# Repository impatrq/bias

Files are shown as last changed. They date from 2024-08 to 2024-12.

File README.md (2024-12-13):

# BIAS: Brain-Intelligence Artificial System
<div style="text-align: center;">
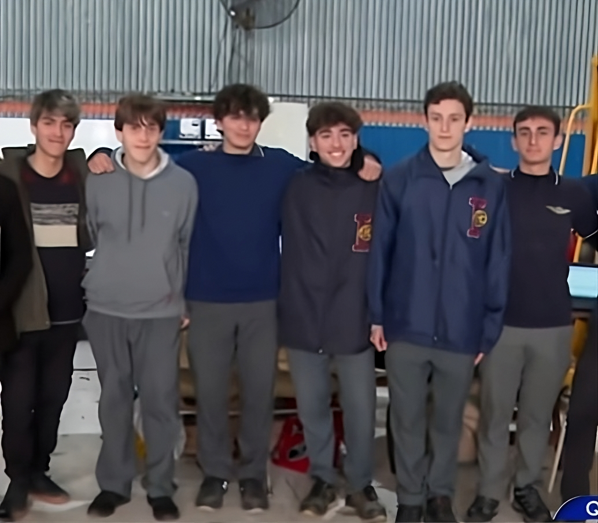
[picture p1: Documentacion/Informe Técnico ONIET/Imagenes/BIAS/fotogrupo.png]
BIAS Grupo
    
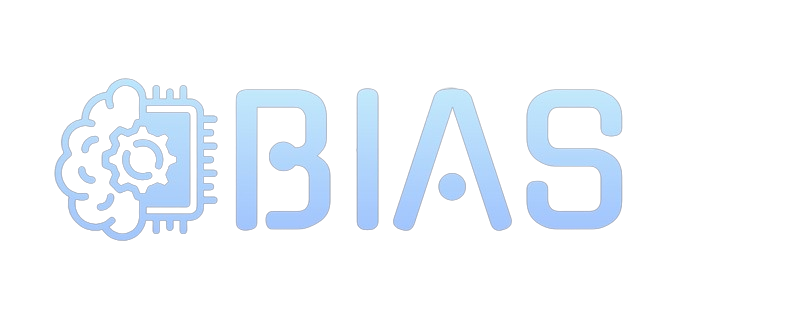
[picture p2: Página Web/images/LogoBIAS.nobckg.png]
BIAS Logo
    
</div>

[Video de Presentación](https://youtu.be/uJyJxOkbonA?si=HoqrQriFnUhKq0Xh)

## Descripción del Proyecto

BIAS es un proyecto innovador que busca mejorar la movilidad de las personas con discapacidades motrices a través de una **silla de ruedas controlada por señales cerebrales**. Utilizamos tecnología de última generación para crear un sistema que interprete las señales eléctricas del cerebro y las traduzca en movimientos precisos para la silla.

## Características principales

- **Control mental**: Movimiento de la silla mediante señales cerebrales captadas por electrodos.
- **Procesador**: Uso de una Raspberry Pi 4 para el procesamiento de las señales.
- **Motor eficiente**: Sistema de motores controlados para movimientos suaves y seguros.
- **Interfaz adaptable**: Personalización según las necesidades del usuario.

## Tecnologías utilizadas

- **Electrodos** para captar las señales cerebrales.
- **Raspberry Pi 4** para el procesamiento de datos.
- **Python y C** para el desarrollo del software y control de la IA.
- **Diseño PCB personalizado** para la integración de los componentes.
- **Motores DC** controlados por puentes H.

## Estructura del Equipo

| Integrante | Responsabilidad |
|---|---|
| **Nicolás Adell** | Programación de la IA y procesamiento de señales |
| **Luca De Blasi** | Código para los motores |
| **Ian Gil Soria** | Diseño de las placas PCB |
| **Danilo Díaz** | Desarrollo de puentes H y drivers de motor |
| **Luciano Montenegro** | Documentación y asistencia técnica |
| **Santiago Sojka** | Marketing, diseño web y estructura de la silla|

## Contacto

- **LinkTree**: [Aquí](https://linktr.ee/biasproject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)
- **Correo**: [bias.project@gmail.com](mailto:https://www.instagram.com/proyecto.bias/)
- **Instagram**: [@proyecto.bias](https://www.instagram.com/proyecto.bias)
- **Pagina Web**: [Aquí](https://sojkaa.github.io/BIAS-WEB/)

*BIAS 2024 - Todos los derechos reservados*

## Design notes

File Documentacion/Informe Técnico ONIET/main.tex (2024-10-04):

\documentclass{article} 
\UseRawInputEncoding
\usepackage[utf8]{inputenc}
\usepackage[T1]{fontenc}
\usepackage{selinput}
\usepackage[spanish]{babel}
\usepackage{hyphenat}
\usepackage{graphicx} 
\usepackage{subcaption}
\usepackage{hyperref}
\usepackage{listings}
\usepackage{xcolor}
\usepackage{float}
\usepackage[a4paper, total={6in, 9in}]{geometry}
\begin{document}
\date{} 

\begin{center}
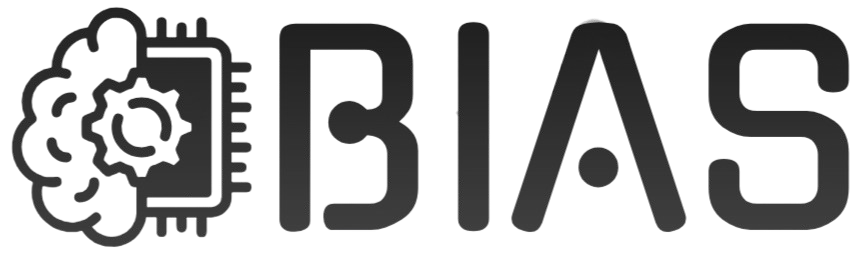
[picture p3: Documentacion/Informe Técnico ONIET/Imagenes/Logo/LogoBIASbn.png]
    \\ 
\end{center}

\title{}

\vspace{1cm} 

\textbf{Integrantes del Proyecto:} 

\begin{itemize}
    \item Adell, Nicolas Fabian (DNI 47020472)
    \item De Blasi, Luca (DNI 47382528)
    \item Diaz Melion, Danilo Sebastian (DNI 47307165)
    \item Gil Soria, Ian Lucas (DNI 47337154)
    \item Montenegro, Luciano Nahuel (DNI 47256543)
    \item Sojka, Santiago Alejandro (DNI 47306441)
\end{itemize}

\begin{figure}[H]
    \centering
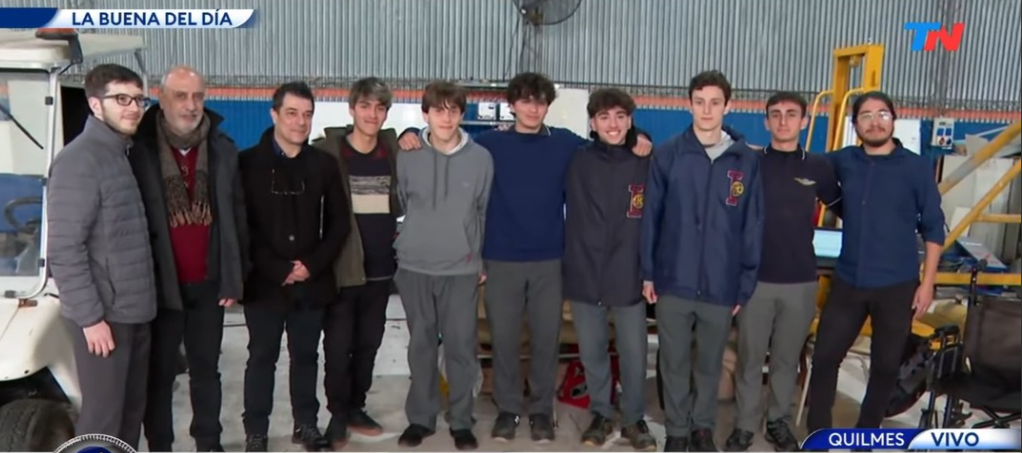
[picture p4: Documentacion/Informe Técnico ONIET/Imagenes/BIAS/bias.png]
    
\end{figure}

\tableofcontents 

\newpage 

\section{Introducción}
El proyecto BIAS es un módulo diseñado para su aplicación en sillas de ruedas, permitiendo al usuario dirigirla mediante el control mental, es decir, a través de sus pensamientos. Con este enfoque, se elimina la necesidad de utilizar un control físico, como el joystick empleado en las sillas eléctricas convencionales. De esta manera, se ofrece mayor independencia y una mejor calidad de vida a personas con movilidad reducida, como aquellos que padecen esclerosis lateral amiotrófica (ELA).

Para su funcionamiento, BIAS emplea una Inteligencia Artificial desarrollada por nuestro equipo, capaz de reconocer los patrones de las señales cerebrales asociadas al movimiento. Estos patrones se traducen en acciones que permiten dirigir la silla en distintas direcciones o, si el usuario así lo desea, mantenerla en su posición actual.

\section{¿Quiénes somos?}
El equipo BIAS (Brain Intelligence Artificial System) está conformado por seis integrantes, todos estudiantes de la Escuela Técnica N° 7 "IMPA" de Quilmes. Actualmente, nos encontramos cursando el séptimo y último año de la educación secundaria, en la especialidad de Aviónica, más específicamente a la segunda división, comisión "C".

\subsection{Metodología de Trabajo}

La metodología aplicada en este proyecto se basa en la organización del equipo en dos grupos especializados. El primer grupo se encarga del desarrollo de los programas, siendo ejemplos de esto los filtros virtuales, programas de recepción y procesado, mientras que el segundo se dedica a la implementación de los motores, sistemas de emergencia y filtros. Esta división del trabajo permite una utilización más eficiente del tiempo, al abordar simultáneamente diversas áreas del proyecto, lo que resulta en un avance más significativo en periodos de tiempo más reducidos.

Dedicamos aproximadamente 30 horas semanales, durante 28 semanas, al desarrollo del proyecto desde principios de marzo, en el contexto de la asignatura "Prácticas Profesionalizantes". Durante este período, todo el tiempo asignado a dicha materia se ha destinado exclusivamente a la planificación, investigación y ejecución de las diferentes etapas del proyecto. En dicha materia, tenemos a cargo a tres profesores, quienes son:

\begin{itemize}
    \item Fabrizio Carlassara
    \item Sergio Medina
    \item Carlos Bianco
\end{itemize}

\section{¿Por qué hacemos este proyecto?}

Como estudiantes de séptimo año, nuestro objetivo es desarrollar un proyecto que cumpla con los requisitos de las prácticas profesionalizantes. Desde un principio, nos propusimos encontrar una iniciativa que generara un impacto social significativo, centrada en mejorar la calidad de vida de personas con discapacidades. En este contexto, y luego de investigar, pensamos en la idea de crear un módulo para sillas de ruedas controlado por la actividad cerebral del usuario, utilizando tecnología de interfaz cerebro-computadora (BCI).

\section{¿A quiénes está dirigido este proyecto?}
Este proyecto está dirigido a personas con movilidad reducida, especialmente aquellos pacientes que presentan una parálisis completa desde el cuello hacia abajo. Entre los principales beneficiarios se encuentran personas que padecen esclerosis lateral amiotrófica (ELA), cuadriplejia, esclerosis múltiple, o aquellos que han sufrido la amputación de extremidades. Dado que el control de la silla de ruedas se realiza a través de señales cerebrales, el alcance del proyecto puede extenderse a una amplia variedad de pacientes con limitaciones motrices de este tipo.

Estamos convencidos de que este proyecto tiene el potencial de transformar la vida de personas con movilidad reducida, permitiéndoles gestionar su propio movimiento y mejorando sustancialmente su calidad de vida, y puede llegar a tener un alcance incluso mundial si es comercializado correctamente.

\section{¿Por qué es innovador este proyecto?}

Consideramos que este proyecto es innovador debido a la escasez de opciones similares en el mercado, sumado a nuestro enfoque en hacerlo accesible para el mayor número posible de personas, facilitando su adquisición por aquellos que lo necesiten. Un aspecto clave de este proyecto es la integración de inteligencia artificial en su funcionamiento, lo que lo diferencia de las soluciones convencionales. Mientras que la mayoría de las sillas de ruedas disponibles se controlan mediante un joystick, esta sería una de las primeras en emplear señales cerebrales para su operación.

La inversión en tiempo y recursos adicionales permitirá perfeccionar sus características técnicas, optimizar su funcionalidad, y adaptar el producto a las necesidades de un mercado que se expande. Una vez finalizado y refinado, el proyecto podrá captar la atención de un público más amplio, lo que incrementará su viabilidad comercial y su posicionamiento en el mercado.

En caso de que el desarrollo del proyecto no se complete en su totalidad, este podrá ser aprovechado por la institución educativa, permitiendo que otros grupos de estudiantes continúen su avance. De esta manera, el proyecto no solo servirá como un recurso valioso para futuras generaciones, sino que también fomentará la colaboración y el aprendizaje continuo dentro de la comunidad académica, garantizando su evolución y finalización.

El presente proyecto tiene como objetivo generar un impacto significativo en la sociedad, fomentando el desarrollo de tecnologías basadas en el control mediante señales cerebrales. Este enfoque tiene el potencial de ampliar las opciones tecnológicas disponibles para personas con limitaciones físicas severas, que les impiden operar dispositivos de manera manual. Con la implementación de este tipo de sistemas, se busca facilitar la creación de soluciones tecnológicas accesibles y eficientes, que permitan a los usuarios controlar una amplia gama de dispositivos mediante interfaces cerebro-computadora (BCI), mejorando así su autonomía y calidad de vida.

\section{Descripción física del proyecto}
En el estado actual del proyecto, el asiento y el motor de la silla de ruedas se encuentran separados. El asiento, fabricado en madera, tiene dimensiones de 65 cm de altura, 40 cm de ancho y 40 cm de profundidad. Por su parte, el motor tiene unas dimensiones de 40 cm de altura, 95 cm de longitud y 70 cm de ancho. Estas especificaciones corresponden a la etapa preliminar del diseño, donde se busca optimizar la integración estructural y funcional de ambos componentes, asegurando tanto la estabilidad del conjunto como su eficiencia operativa.

\begin{figure}[H]
    \centering
    
    \caption{Asiento de la silla de ruedas}
\end{figure}

\begin{figure}[H]
    \centering
    
    \caption{Motor de la silla de ruedas}
\end{figure}

\section{Investigaciones realizadas}

Para concretar la idea principal del proyecto y dar inicio a su desarrollo, se realizaron investigaciones exhaustivas en diversas áreas. Estas incluyeron el análisis de proyectos similares, como el de la silla de ruedas controlada por la mente conocida como Milo, así como estudios más específicos sobre componentes técnicos clave, tales como el puente H de potencia, los filtros, y el sistema de compensación de offset. También se llevó a cabo una investigación detallada sobre dispositivos EEG, como el NeuroSky, que inicialmente fue utilizado pero posteriormente descartado. Además, se profundizó en el estudio de las señales cerebrales y los métodos para su medición. Como parte del proceso, nos contactamos con diversas fundaciones y expertos en el área, con el objetivo de obtener información adicional y recibir apoyo en la implementación del proyecto.

\section{Descripción del funcionamiento}
El usuario se sienta en la silla de ruedas y se coloca el dispositivo EEG. El EEG capta las señales cerebrales y las somete a un proceso de filtrado por hardware de varias etapas. Luego, las envía a un circuito de compensación de Offset, para que la RP2040 Zero pueda leerlas. Estos datos, se los envía a la Raspberry Pi 4, en donde está el programa principal de la silla de ruedas.

En esta placa se encuentran los filtros digitales, el programa para el control de los motores, el procesamiento de señales y la inteligencia artificial. Una vez que las señales llegan a la Raspberry Pi 4, se las filtra digitalmente para eliminar el ruido de las señales. Luego de ser filtradas, se las envía a la IA, que reconoce los patrones cerebrales, y dependiendo de a dónde se quiera mover el usuario, enviará una señal a los motores en la dirección deseada, ya sea hacia adelante, detrás, izquierda, derecha o mantenerse en el lugar.

\subsection {Informacion Adicional}
La silla desarrollada en este proyecto es un prototipo, es decir, puede contener fallas de todo tipo, y es sujeto a modificaciones a futuro. Se recomienda su uso siempre acompañado, en zonas amplias libres de obstáculos. No se debe usar en lugares húmedos o si el equipo está mojado, y la inteligencia artificial está adaptada a las muestras de una persona del equipo del proyecto, por lo que para ser usada por alguien mas se deberán muestrear los patrones de movimiento de esta misma.

En caso de que haya un error en la lectura de señales o haya un obstáculo en la trayectoria de la silla, se activará un sistema de emergencia. Su objetivo es prevenir accidentes y brindarle mayor seguridad al usuario. El sistema frena los motores y enciende un LED en la dirección del obstáculo, y enciende un buzzer, que enciende una señal sonora.

\subsubsection{¿Que es un EEG?}

Un electroencefalógrafo es un dispositivo médico que se utiliza para registrar y medir la actividad eléctrica del cerebro. Su función principal es captar las señales eléctricas generadas por las neuronas cerebrales y transformarlas en gráficos de ondas cerebrales, que se pueden analizar para evaluar la función cerebral.

\subsubsection{Componentes que tiene un EEG}
\begin{itemize}
    \item \textbf{Electrodos:} Pequeños sensores que se colocan en el cuero cabelludo para captar los cambios de voltaje producidos por la actividad cerebral.
    \item \textbf{Amplificador:} Como las señales eléctricas del cerebro son muy débiles, el electroencefalógrafo incluye amplificadores que aumentan la señal para que sea lo suficientemente fuerte como para ser registrada.
    \item \textbf{Conversor analógico-digital:} Convierte las señales eléctricas captadas en un formato digital para su procesamiento por computadora.
    \item \textbf{Software de procesamiento:} El dispositivo utiliza un software que transforma las señales en gráficos de ondas cerebrales que se presentan en tiempo real en una pantalla o se registran para análisis posterior.
    \item \textbf{Pantalla/Gráficos:} El electroencefalógrafo muestra las señales eléctricas en forma de ondas, conocidas como ondas cerebrales (Delta, Theta, Alpha, Beta, Gamma), lo que permite a los médicos interpretar la actividad cerebral.
\end{itemize}

\subsubsection{¿Cómo se aplican los electrodos?}

El sistema 10-20 es un método internacionalmente estandarizado para la colocación de electrodos en el cuero cabelludo durante un electroencefalograma (EEG). Este sistema asegura que los electrodos se coloquen de manera uniforme y precisa en relación con los puntos anatómicos del cráneo, permitiendo una medición consistente y reproducible de la actividad eléctrica cerebral.

El sistema 10-20 se utiliza para garantizar una colocación precisa y consistente de los electrodos en los estudios de EEG. Algunos de sus beneficios incluyen:

\begin{itemize}
    \item \textbf{Estandarización global:} Permite que los estudios de EEG sean comparables en diferentes laboratorios y entre diferentes pacientes.
    \item \textbf{Cobertura completa del cerebro:} El sistema asegura que se cubran adecuadamente diferentes áreas del cerebro (frontal, parietal, occipital, temporal).
    \item \textbf{Detección de anomalías:} Facilita la identificación de regiones del cerebro donde pueden estar ocurriendo fenómenos anormales, como descargas epilépticas, actividad lenta anormal o asimetrías en las ondas cerebrales.
\end{itemize}

El nombre "10-20" proviene de las distancias porcentuales entre los electrodos: Los electrodos se colocan en posiciones que están al 10\% o al 20\% de la distancia total entre puntos anatómicos clave del cráneo.
Puntos anatómicos clave de referencia:

\begin{itemize}

    \item \textbf{Nasion:} El punto entre la frente y la nariz.
    
    \item \textbf{Inion:} El punto más prominente en la parte posterior de la cabeza.
    
    \item \textbf{Puntos preauriculares:} Justo por encima de los oídos, a cada lado de la cabeza.
    
\end{itemize}

Las posiciones de los electrodos se distribuyen sobre la cabeza tomando como referencia estos puntos para cubrir todo el cuero cabelludo de forma equidistante.

En la siguiente imágen se puede visualizar de mejor manera la posición de los electrodos:

\begin{figure}[H]

    \centering
    
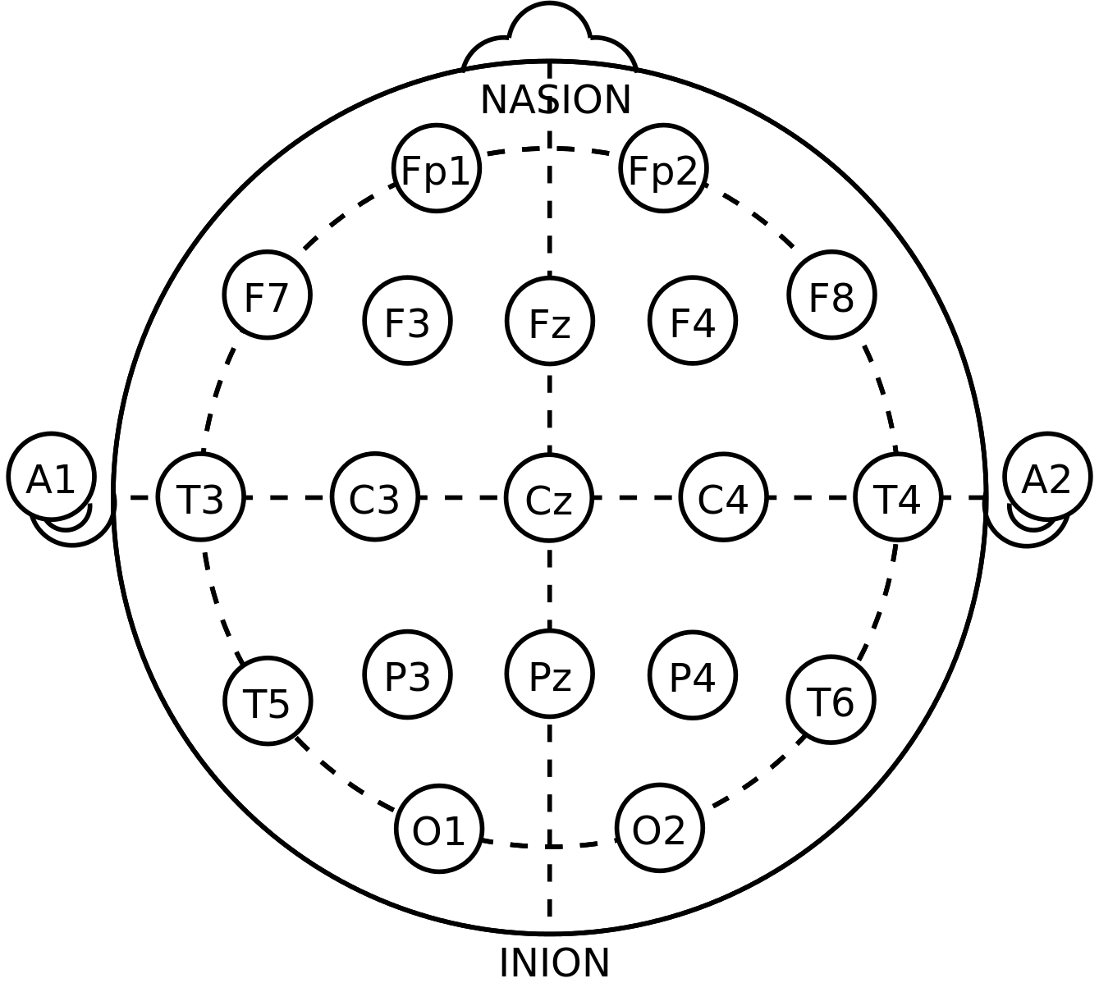
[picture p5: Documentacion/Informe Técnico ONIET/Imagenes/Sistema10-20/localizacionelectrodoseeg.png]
    
    \caption{Sistema 10-20}
    
\end{figure}

\subsubsection{Pasos para aplicar el sistema 10-20}

\begin{enumerate}

    \item \textbf{Medición del cráneo:} Se mide la distancia desde el nasion al inion y desde un punto preauricular al otro. Luego, se calculan los puntos intermedios en un 10 o 20 de esas distancias para determinar las ubicaciones exactas de los electrodos.
    
    \item \textbf{Colocación de los electrodos:} Se colocan electrodos en los puntos marcados, asegurando una cobertura uniforme de la cabeza. Esto puede hacerse usando una gorra de EEG con posiciones ya marcadas o mediante la medición manual.
    
    \item \textbf{Registro de la actividad:} Una vez colocados los electrodos, se inicia el registro de la actividad cerebral. Los electrodos miden las diferencias de potencial eléctrico entre las regiones del cerebro cubiertas por los electrodos.
    
\end{enumerate}

\section{Desarrollo Técnico}
En esta sección se desarrollarán y explicarán los distintos circuitos que conforman el dispositivo, así como los datos necesarios para comprender su funcionamiento y mantenimiento.

\subsection{Funcionamiento del EEG}

El sistema de control de nuestra silla de ruedas se basa en el reconocimiento de señales cerebrales, lo que requiere un dispositivo especializado para captarlas: el electroencefalograma (EEG). Hemos desarrollado un EEG en forma de una cofia equipada con electrodos, los cuales se colocan siguiendo el protocolo conocido como “Sistema 10-20”. Este sistema estándar de ubicación define puntos específicos en el cuero cabelludo donde se deben colocar los electrodos para obtener lecturas óptimas de la actividad cerebral.

Los electrodos actúan como sensores pasivos que detectan las ondas cerebrales producidas por la actividad eléctrica del cerebro. Estas ondas se manifiestan como pequeñas fluctuaciones en el voltaje, que son captadas por los electrodos cuando se colocan sobre la superficie del cuero cabelludo del usuario. Es importante destacar que estos electrodos no penetran en el cráneo ni interactúan directamente con las neuronas. En cambio, registran los potenciales eléctricos generados por la actividad cerebral subyacente que se propagan hasta la superficie del cuero cabelludo.

Debido a que las señales captadas por los electrodos son de muy baja amplitud, requieren ser amplificadas antes de su procesamiento. Este paso no solo amplifica la señal cerebral, sino también el ruido presente en el entorno o generado por el propio cuerpo. Para abordar este problema, se realiza un proceso de filtrado que elimina el ruido y permite aislar las frecuencias relevantes de las ondas cerebrales.

Las frecuencias de las ondas cerebrales detectadas son las siguientes:

\begin{itemize}
    \item Ondas alfa: 8-12 Hz
    \item Ondas beta: 12-30 Hz
    \item Ondas gamma: 30-100 Hz
    \item Ondas delta: 0,5-4 Hz
    \item Ondas theta: 4-8 Hz
\end{itemize}

Estas ondas cerebrales están asociadas con diferentes estados mentales y actividades cerebrales, por ejemplo, las ondas alfa se observan comúnmente en estados de relajación, mientras que las ondas beta se relacionan con un estado de alerta y concentración. Las ondas gamma, por otro lado, están vinculadas a procesos cognitivos de mayor complejidad, como la percepción y la conciencia. Las ondas delta y theta se asocian con fases profundas del sueño y la meditación.

\subsection{Funcionamiento de los filtros HardWare}

En un sistema de EEG, después de amplificar las señales captadas por los electrodos, se utilizan varios filtros para limpiar y mejorar la calidad de las señales antes de procesarlas o analizarlas. Estos filtros tienen un propósito importante: eliminar el ruido y enfocarse en las señales cerebrales relevantes. 

\subsubsection{Filtro Notch de 50 Hz}

\begin{itemize}

    \item \textbf{Propósito:} Atenuación del ruido inducido por la red eléctrica de 50 Hz, común en muchos sistemas de distribución de energía.
    
    \item \textbf{Funcionamiento:} El filtro Notch es un filtro de rechazo de banda estrecha, diseñado para eliminar una frecuencia específica (en este caso, 50 Hz) sin afectar significativamente las componentes de frecuencia cercanas o las señales EEG de interés. Las señales de EEG, que suelen estar en el rango de 0,5 a 40 Hz, pueden contaminarse por la interferencia de la red, por lo que este filtro resulta esencial para su eliminación sin alterar la información relevante.
    
\end{itemize}

\subsubsection{Filtro pasa bajos de 100 Hz}

\begin{itemize}

    \item \textbf{Propósito:} Reducción de las componentes de alta frecuencia que no son relevantes para el análisis EEG.
    
    \item \textbf{Funcionamiento:} Este filtro pasa bajos permite el paso de frecuencias inferiores a 100 Hz, atenuando aquellas que exceden este umbral. Las señales cerebrales de interés generalmente se sitúan por debajo de los 40 Hz, aunque algunas pueden extenderse hasta 100 Hz. Este filtro elimina frecuencias más altas, que usualmente corresponden a interferencias electromagnéticas, ruido de dispositivos electrónicos o artefactos musculares (EMG).
    
\end{itemize}

\subsubsection{Filtro pasa altos de 0,5 Hz}

\begin{itemize}

    \item \textbf{Propósito:} Eliminación de las componentes de muy baja frecuencia, incluyendo artefactos de corriente continua (DC) y ruido de baja frecuencia no relacionado con la actividad cerebral.
    
    \item \textbf{Funcionamiento:} El filtro pasa altos atenúa las señales con frecuencias por debajo de 0,5 Hz, permitiendo únicamente el paso de frecuencias superiores. La señal EEG relevante generalmente comienza en torno a los 0,5 Hz, mientras que frecuencias menores suelen estar asociadas a artefactos como el desplazamiento de los electrodos, fluctuaciones en la impedancia de los mismos, o interferencias lentas que no contienen información útil sobre la actividad cerebral.
    
\end{itemize}

\subsection{Funcionamiento de los filtros digitales}

Una vez que las ondas cerebrales son captadas y sometidas a un proceso inicial de filtrado, son transferidas a una Raspberry Pi 4. En este dispositivo se ejecuta un programa, desarrollado íntegramente por nuestro equipo, que continúa con el procesamiento y refinamiento de la señal. El motivo por el cual se aplica un filtrado adicional es que, luego de la etapa de filtrado inicial, la señal pasa por un segundo amplificador. Este amplificador, además de amplificar las señales cerebrales de interés, también amplifica el ruido residual presente en las mismas. Para contrarrestar este efecto, empleamos filtros digitales implementados por software, los cuales ofrecen una mayor precisión y control en la eliminación de interferencias no deseadas.

Dentro del programa, se han implementado los siguientes filtros:

\begin{itemize}

    \item \textbf{Filtro Notch de 50 Hz:} Este filtro está diseñado para eliminar las interferencias generadas por la red eléctrica, las cuales operan a una frecuencia de 50 Hz. Dado que estas interferencias pueden superponerse con la señal cerebral y distorsionar su interpretación, su eliminación es esencial para obtener un registro más fiel de la actividad cerebral.
    
    \item \textbf{Filtro Pasa-Bajo de 100 Hz:} El objetivo de este filtro es retener las frecuencias cerebrales más relevantes, es decir, aquellas que se encuentran por debajo de los 100 Hz, mientras que elimina el ruido de alta frecuencia, que suele ser resultado de interferencias externas o artefactos no relacionados con la actividad cerebral. Este rango incluye frecuencias relacionadas con ritmos cerebrales importantes como las ondas alfa, beta, y gamma.
    
    \item \textbf{Filtro Pasa-Alto de 0,5 Hz:} Este filtro se encarga de remover las señales de baja frecuencia que no aportan información útil sobre la actividad cerebral, como los artefactos causados por movimientos lentos o variaciones de corriente. Solo se permite el paso de las frecuencias EEG relevantes, garantizando que las señales reflejen con mayor precisión la actividad neural de interés.
    
\end{itemize}

Es importante señalar que el uso de estos filtros garantiza que la señal procesada esté lo más limpia posible de interferencias y artefactos, mejorando la precisión del sistema para detectar y procesar patrones cerebrales. La implementación de filtros mediante software, además, permite ajustar dinámicamente las configuraciones según las necesidades específicas del sistema y del entorno operativo, optimizando así el rendimiento de la silla de ruedas controlada por señales cerebrales.

\subsection{Funcionamiento del Puente H}

Un Puente H es un circuito utilizado para invertir el sentido de giro de un motor y para separar su etapa de potencia con la de control. Su nombre viene de la forma gráfica que tiene el circuito. Se construye con 4 interruptores, pueden ser mecánicos o transistores.

Nosotros optamos por diseñar un puente H de potencia, el cual es un tipo de circuito en el que la etapa de potencia, que incluye el motor, los transistores y está conectada a altas tensiones y corrientes, se encuentra separada de la etapa de control, la cual generalmente opera con voltajes más bajos. Esta separación se realiza para proteger la etapa de control de las altas tensiones, que podrían dañar o quemar sus circuitos.

El circuito que creamos utiliza dos señales PWM (PWM1 y PWM2) para controlar los transistores MOSFET en configuración de puente H, lo que permite invertir la polaridad del voltaje aplicado al motor, controlando así la dirección de rotación. 

La velocidad del motor puede controlarse ajustando el ciclo de trabajo (duty cycle) de las señales PWM, que modulan la cantidad de energía entregada al motor.

\subsubsection{Descripción de los Componentes}

\begin{enumerate}

    \item \textbf{U1 y U2 (PC817 - Optoacopladores):} Aíslan eléctricamente el circuito de control (de baja tensión) del circuito de potencia (de alta tensión). Esto protege al microcontrolador de posibles picos de voltaje y ruidos eléctricos provenientes del circuito de potencia.
    Cada optoacoplador tiene un LED interno que, al ser activado por una señal PWM, enciende un fototransistor interno, permitiendo que la señal de control pase al lado de potencia.
    
    \item \textbf{Q1 y Q3 (IRF4905 - MOSFET canal P):} Actúan como interruptores en la parte superior del puente H. Controlan la alimentación positiva hacia el motor. Estos MOSFET se activan cuando la señal PWM1 o PWM2 está en bajo (0V) y se desactivan cuando está en alto (señal de 5V), debido a la naturaleza de los MOSFET de canal P.
    
    \item \textbf{Q2 y Q4 (IRF2805 - MOSFET canal N):} Actúan como interruptores en la parte inferior del puente H. Conectan el motor a tierra cuando están activados. Estos MOSFET se activan cuando la señal PWM1 o PWM2 está en alto (5V) y se desactivan cuando está en bajo (0V).
    
    \item \textbf{R1 y R2 (Resistencias de 180 ohms):} Limitan la corriente de entrada hacia los LEDs internos de los optoacopladores (U1 y U2) para protegerlos de daños.
    
    \item \textbf{R3 y R4 (Resistencias de 1k ohms):} Están conectadas en serie con los MOSFET de canal P (Q1 y Q3). Limitan la corriente de la compuerta y aseguran un apagado rápido del MOSFET al detenerse la señal.
    
    \item \textbf{J1 y J2 (Conectores de entrada PWM):} Reciben las señales PWM de control provenientes de un microcontrolador o una fuente de señal PWM.
    
    \item \textbf{J3 y J4 (Conectores de alimentación):} Proveen la alimentación al circuito, uno con 24V para el motor y otro con 15V para los circuitos de control.
    
    \item \textbf{SW1 (Interruptor):}  utilizado para habilitar o deshabilitar el circuito completo, conectando o desconectando GND.

\end{enumerate}

\section{Circuitos usados}
En este capítulo se incluirán imágenes de los esquemas de los circuitos, junto con su representación gráfica en formato virtual de los circuitos impresos, así como fotografías de los circuitos completos una vez finalizados.

\subsection{Esquemático de los filtros}
\begin{figure}[H]
    \centering
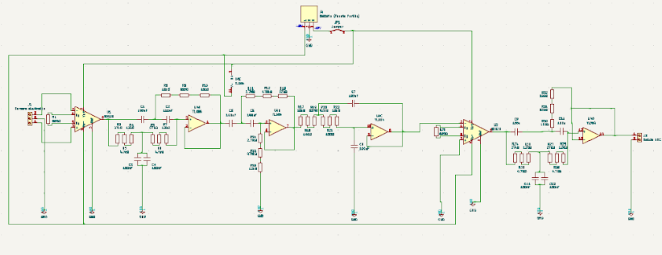
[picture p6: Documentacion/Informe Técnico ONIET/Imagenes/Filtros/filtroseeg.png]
    
    \caption{Esquemático de los filtros del EEG}
\end{figure}

\subsection{Esquemático del sistema de control}
\begin{figure}[H]
    \centering
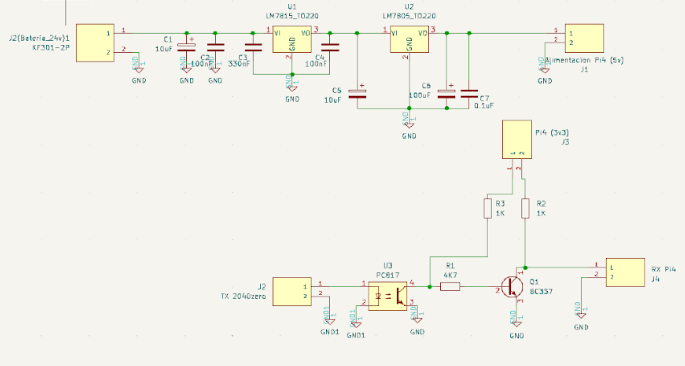
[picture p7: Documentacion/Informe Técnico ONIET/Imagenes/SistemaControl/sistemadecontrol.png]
    
    \caption{Esquemáticos del sistema de control}
\end{figure}

\subsection{Esquemático del sistema Offset}
\begin{figure}[H]
    \centering
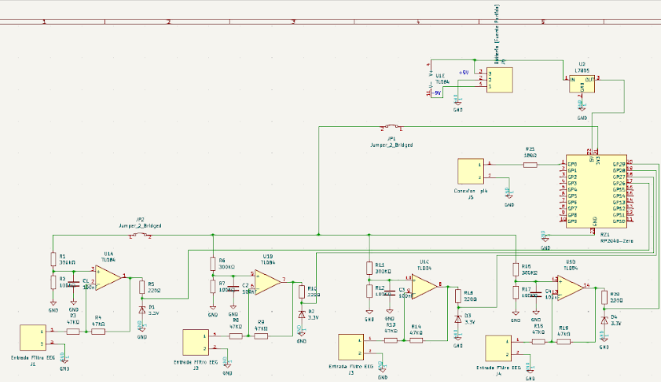
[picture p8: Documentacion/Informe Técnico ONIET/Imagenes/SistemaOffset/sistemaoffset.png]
    
    \caption{Esquemático del sistema de Offset}
\end{figure}

\subsection{Esquemáticos de los Puentes H}
\begin{figure}[H]
    \centering
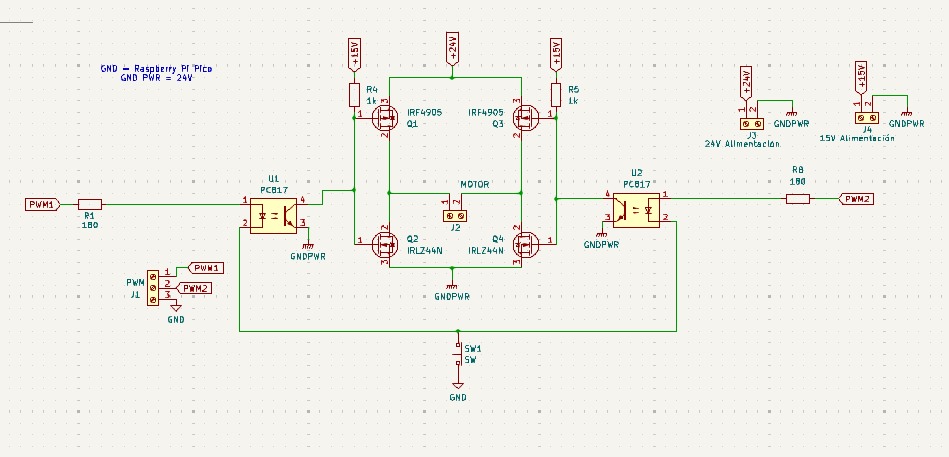
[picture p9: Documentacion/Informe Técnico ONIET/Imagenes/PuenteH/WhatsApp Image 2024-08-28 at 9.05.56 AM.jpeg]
     
    \caption{Puente H (Un Motor)}
\end{figure}

\subsection{Esquemático del sistema de emergencia}
\begin{figure}[H]
    \centering
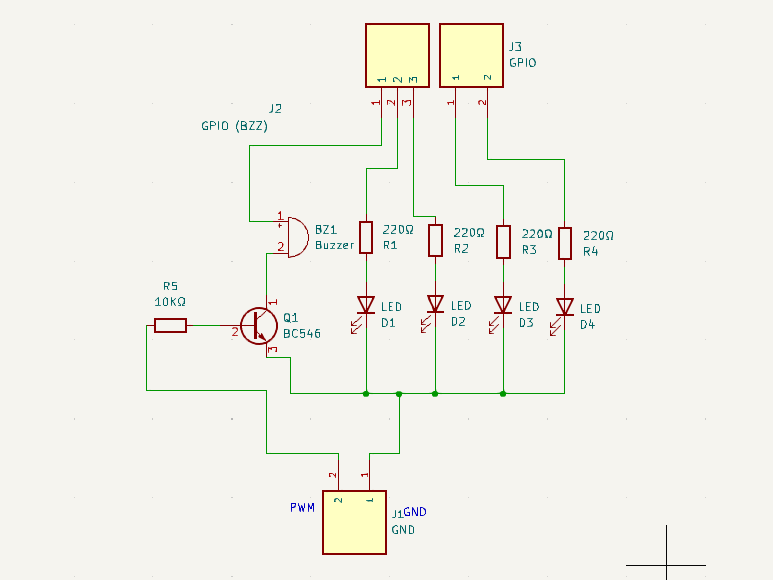
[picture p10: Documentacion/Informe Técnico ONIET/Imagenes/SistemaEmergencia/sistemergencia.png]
    
    \caption{Esquemático del sistema de emegencia}

    \begin{subfigure}[t]{0.5\textwidth}
        \centering
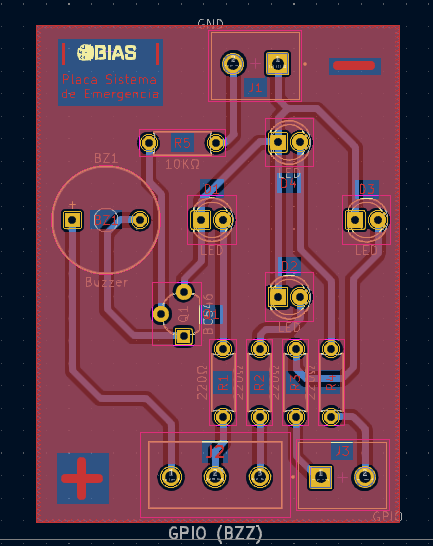
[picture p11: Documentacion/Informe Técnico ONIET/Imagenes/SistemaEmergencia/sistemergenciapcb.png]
        
        \caption{PCB Del sistema de emergencia}
    \end{subfigure}%
    ~ 
    \begin{subfigure}[t]{0.5\textwidth}
        \centering
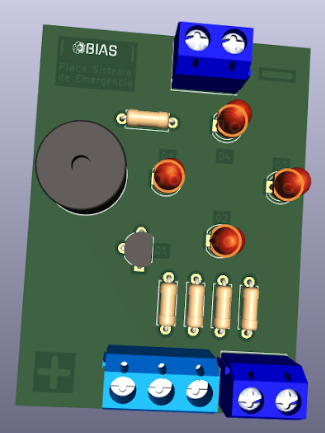
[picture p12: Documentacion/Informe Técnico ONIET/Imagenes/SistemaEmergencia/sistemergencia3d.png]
        
        \caption{Modelo 3D Del sistema de emergencia}
    \end{subfigure}

\end{figure}

\newpage

\section{Agradecimientos}
Queremos expresar nuestro más profundo agradecimiento a los profesores que nos han brindado su invaluable apoyo en la realización de este proyecto:

\begin{itemize}

    \item Fabrizio Carlassara: Su asistencia fue crucial en la programación de la mayor parte del proyecto, así como en la creación de circuitos y esquemáticos, la búsqueda de materiales y el desarrollo de los filtros necesarios.

    \item Sergio Medina: Nos brindó su experiencia en la presentación y comercialización del proyecto, además de colaborar en la programación, la búsqueda de materiales y la planificación de los puentes H.

    \item Carlos Bianco: Su apoyo fue esencial en las pruebas y acondicionamiento de los motores, proporcionándonos herramientas y baterías para dichas pruebas, además de colaborar en la búsqueda de materiales.

    \item Daniel Espósito: Nos proporcionó motores y materiales, además de enseñarnos a construir los puentes H para los motores y nos ayudó a solucionar problemas con las pistas de los circuitos para las altas corrientes.

    \item Federico Solomiewicz: Colaboró principalmente en el desarrollo de los filtros, proporcionándonos herramientas para el proyecto y estando siempre disponible para resolver cualquier duda que surgiera.

    \item Juan Carlos Ruiz: Su colaboración fue esencial en las pruebas de los motores para la silla de ruedas, además de ayudarnos principalmente en la creación de los puentes H para los motores y sus circuitos impresos.

\end{itemize}
\end{document}

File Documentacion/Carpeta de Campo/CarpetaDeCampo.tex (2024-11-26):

\documentclass{article} 
\UseRawInputEncoding
\usepackage[utf8]{inputenc}
\usepackage[T1]{fontenc}
\usepackage{selinput}
\usepackage[spanish]{babel}
\usepackage{hyphenat}
\usepackage{graphicx} 
\usepackage{subcaption}
\usepackage{hyperref}
\usepackage{listings}
\usepackage{xcolor}
\usepackage{float}
\usepackage[a4paper, total={6in, 9in}]{geometry}
\SelectInputMappings{%
  eacute={é},
}

\definecolor{codegreen}{rgb}{0,0.6,0}
\definecolor{codegray}{rgb}{0.5,0.5,0.5}
\definecolor{codepurple}{rgb}{0.58,0,0.82}
\definecolor{backcolour}{rgb}{0.95,0.95,0.92}

\lstdefinestyle{mystyle}{
    backgroundcolor=\color{backcolour},
    commentstyle=\color{codegreen},
    keywordstyle=\color{blue},
    numberstyle=\tiny\color{codegray},
    stringstyle=\color{codepurple},
    basicstyle=\ttfamily\footnotesize,
    breakatwhitespace=false,
    breaklines=true,
    captionpos=b,
    keepspaces=true,
    numbers=left,
    numbersep=5pt,
    showspaces=false,
    showstringspaces=false,
    showtabs=false,
    tabsize=2
}

\lstdefinelanguage{CSS}{
  keywords={color,background-image:,margin,padding,font,weight,display,position,top,left,right,bottom,list,style,border,size,white,space,min,width, transition:, transform:, transition-property, transition-duration, transition-timing-function},	
  sensitive=true,
  morecomment=[l]{//},
  morecomment=[s]{/*}{*/},
  morestring=[b]',
  morestring=[b]",
  alsoletter={:},
  alsodigit={-}
}
\lstset{style=mystyle}
\title{Carpeta de Campo BIAS}

\date{}

\begin{document}

\begin{figure}
    \centering
    
\end{figure}

\maketitle

\vspace{1cm} 

\textbf{Integrantes del Proyecto:} 

\begin{itemize}
    \item Adell, Nicolas Fabian
    \item De Blasi, Luca
    \item Diaz Melion, Danilo Sebastian
    \item Gil Soria, Ian Lucas
    \item Montenegro, Luciano Nahuel
    \item Sojka, Santiago Alejandro
\end{itemize}

\newpage

\subsection{Adell, Nicolás Fabián}

\begin{figure}[H]
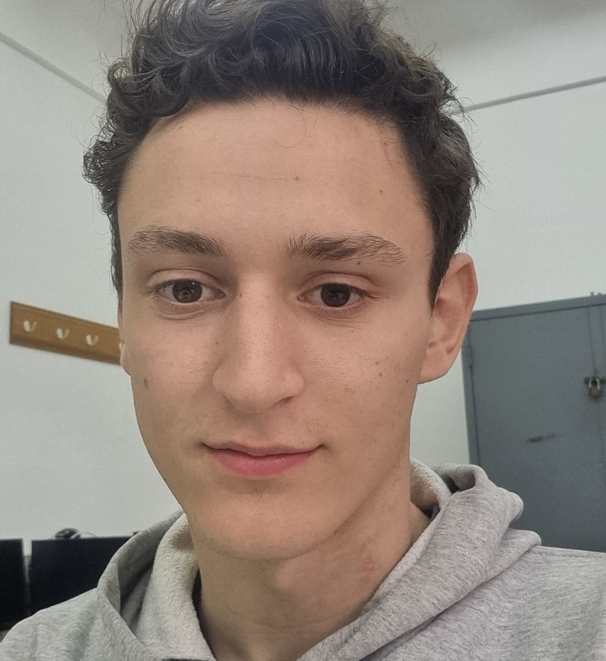
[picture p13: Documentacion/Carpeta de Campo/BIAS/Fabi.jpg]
    
\end{figure}

\subsection{De Blasi, Luca}

\begin{figure}[H]
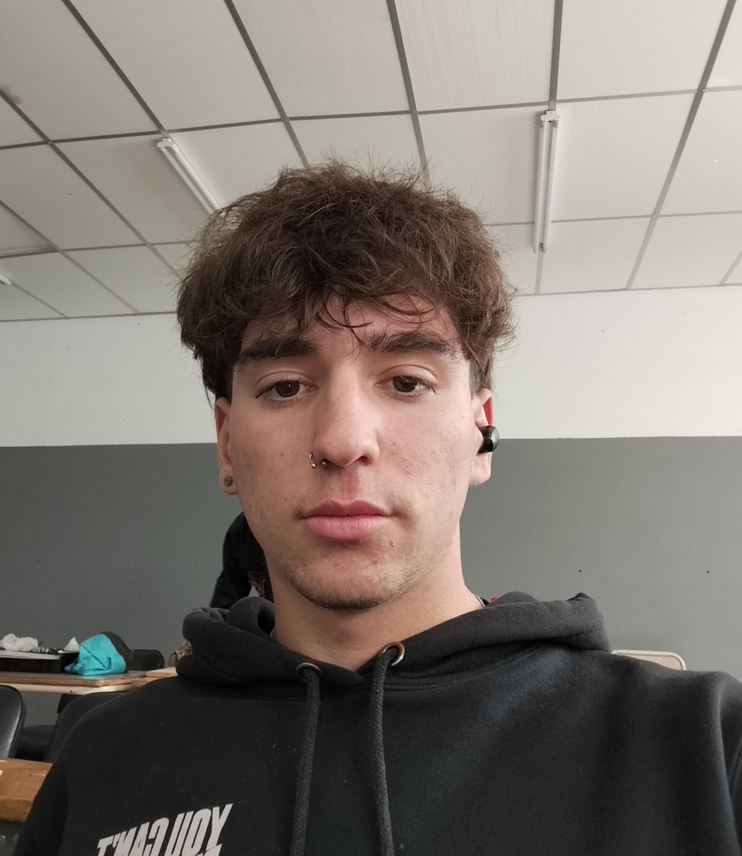
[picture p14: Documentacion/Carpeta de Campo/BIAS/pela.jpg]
    
\end{figure}

\subsection{Diaz Melión, Danilo Sebastián}

\begin{figure}[H]
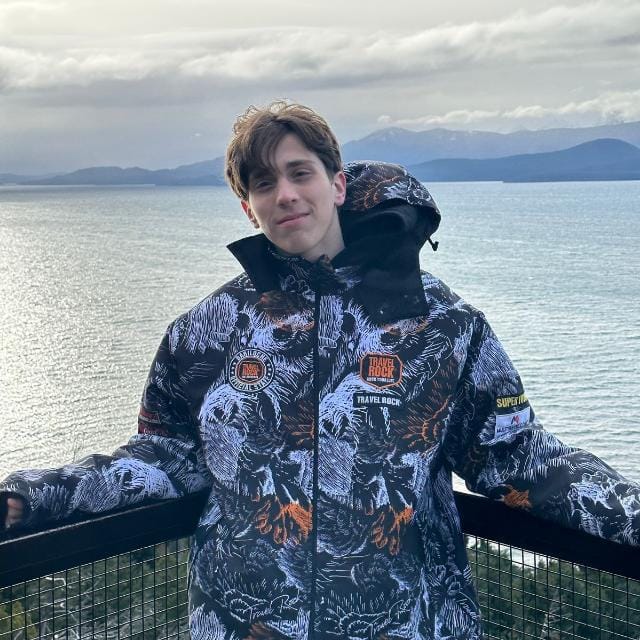
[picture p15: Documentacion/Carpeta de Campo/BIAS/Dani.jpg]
    
\end{figure}

\subsection{Gil Soria, Ian Lucas}

\begin{figure}[H]
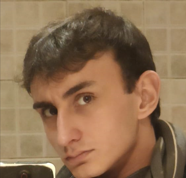
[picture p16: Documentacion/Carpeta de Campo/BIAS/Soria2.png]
    
\end{figure}

\subsection{Montenegro, Luciano Nahuel}

\begin{figure}[H]
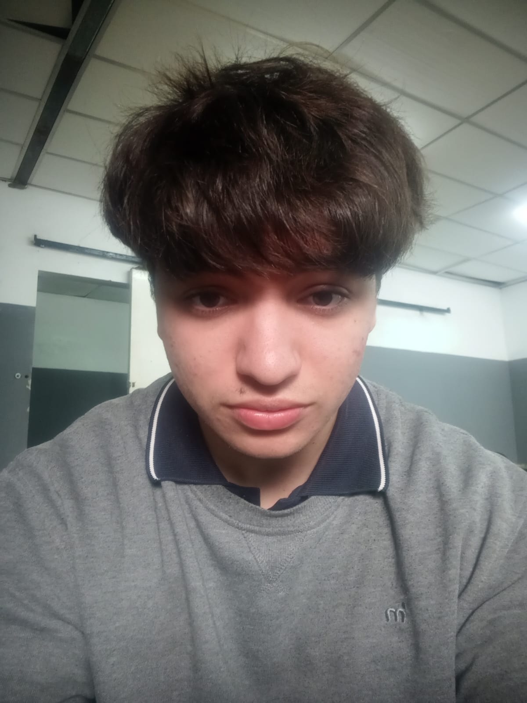
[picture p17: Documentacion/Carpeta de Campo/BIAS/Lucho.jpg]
    
\end{figure}

\subsection{Sojka, Santiago Alejandro}

\begin{figure}[H]
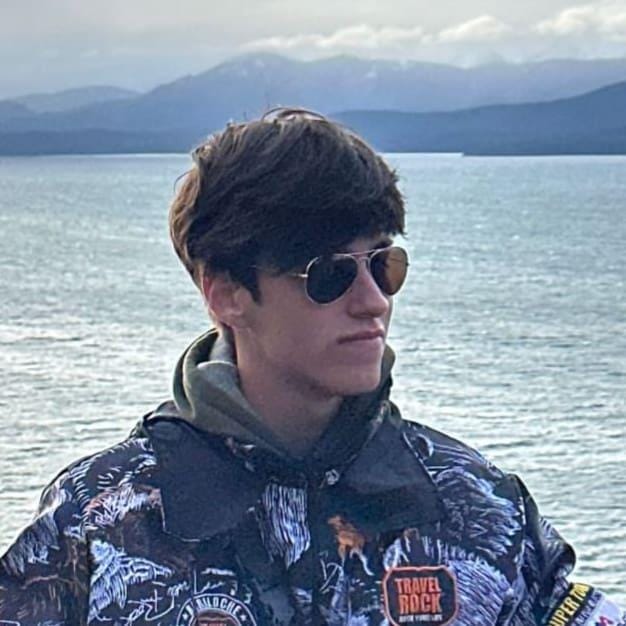
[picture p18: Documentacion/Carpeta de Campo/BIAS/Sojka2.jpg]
    
\end{figure}

\newpage

\section{Marzo de 2024}

Inicio de anteproyecto e investigación sobre la utilización de MATLAB, Python y cómo vincular el Neurosky Mindwave Mobile 2 a una computadora o celular. Decisión de elección de microcontrolador y hardware a utilizar.

\begin{center}
    \href{https://theses.hal.science/tel-04011453v1/document}{https://theses.hal.science/tel-04011453v1/document}
\end{center}

Realización y testeo del código para poder mover la silla de ruedas mediante un joystick.
Investigación sobre los posibles materiales a utilizar en el proyecto ya existentes en la escuela. Hemos visto las posibles sillas de ruedas a utilizar en el proyecto.
Investigación del sensor ultrasónico a utilizar en el proyecto.

Hemos empezado a realizar la programación de los motores y la programación del ultrasonido y se han probado en protoboard, probando que funcionan. También se han hecho ciertas modificaciones al anteproyecto, y se ha empezado a hacer el diagrama temporal. 

\begin{figure}[H]
    \centering
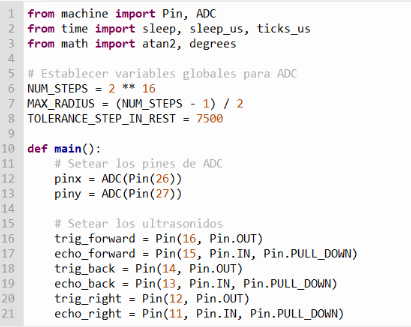
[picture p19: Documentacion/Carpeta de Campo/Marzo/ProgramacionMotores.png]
    
\end{figure}

\newpage

Hemos hecho el logo del proyecto, hemos encontrado las baterías necesarias para poder mover la silla de ruedas, discutimos, tanto entre nosotros como con otros profesores, sobre la utilización de 1 o 2 motores, discutimos sobre los drivers y el puente H.

\begin{figure}[H]
    \centering
    
\end{figure}

En el día de la fecha hemos creado la cuenta  de la red social instagram junto al mail mismo del proyecto.

\begin{figure}[H]
    \centering
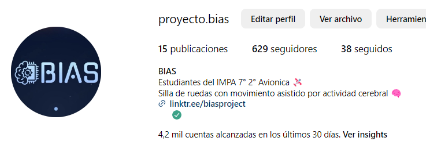
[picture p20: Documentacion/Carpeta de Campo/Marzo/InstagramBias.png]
    
\end{figure}

Hemos realizado el esquemático junto al diseño del pcb del sistema de emergencias, por lo que quedaría imprimirlo y ya ir armando la placa.

\begin{figure}[H]
    \centering
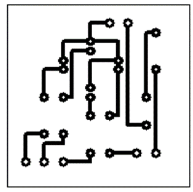
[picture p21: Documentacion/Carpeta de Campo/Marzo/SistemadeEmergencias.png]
    
\end{figure}

\newpage

Investigamos la datasheet del driver del motor, empezamos a investigar el circuito interno y las posibilidades a la hora de manejar el motor.

\begin{figure}[H]
    \centering
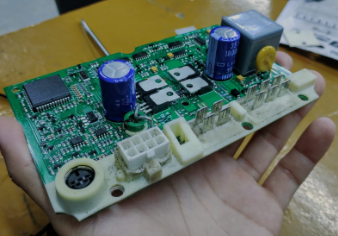
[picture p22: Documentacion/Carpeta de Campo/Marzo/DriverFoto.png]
    
\end{figure}

Empezamos a desarrollar el programa para conectar el Neurosky a un módulo HC-05.

\begin{figure}[H]
    \centering
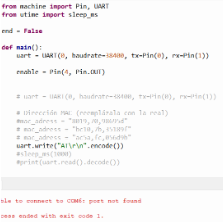
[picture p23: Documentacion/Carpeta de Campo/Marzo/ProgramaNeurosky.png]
    
\end{figure}

\newpage

\begin{center}
    \section{Abril de 2024}
\end{center}

Hemos empezado a organizarnos con la plataforma trello para tener buena percepción sobre las tareas a realizar.

\begin{figure}[H]
    \centering
    
\end{figure}

Estuvimos buscando la forma de conectar el Neurosky a la computadora a través de bluetooth, y terminamos optando por seguir con el HC-05, ya que no se conecta directamente y las versiones no son compatibles.

\begin{figure}[H]
    \centering
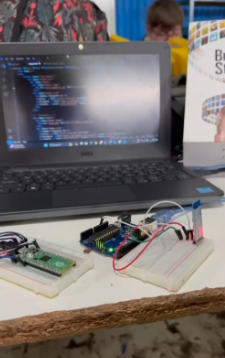
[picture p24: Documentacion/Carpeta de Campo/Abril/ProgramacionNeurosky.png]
    
\end{figure}

\newpage

Hicimos las imágenes que vamos a publicar al Instagram a la hora de que verifiquen el LinkedIn, seguimos desarrollando el programa para usar el módulo bluetooth (HC-05), empezamos a hacer un plano de la silla de ruedas para hacer las modificaciones de la estructura que tengamos que hacer.

\begin{figure}[H]
    \centering
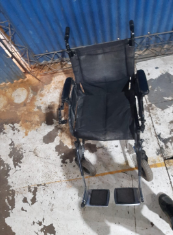
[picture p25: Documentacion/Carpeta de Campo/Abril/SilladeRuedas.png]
    
\end{figure}

Se consiguió con éxito poder establecer la conexión Bluetooth del HC05 a una computadora 

\begin{figure}[H]
    \centering
    
\end{figure}

\newpage

Cargamos las baterías y empezamos a probar los motores junto al driver, investigamos sobre otras opciones para reemplazar al Neurosky, ya que no hay forma de hacerlos vincular..

\begin{figure}[H]
    \centering
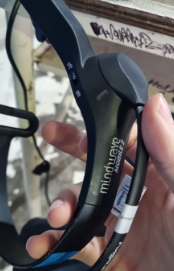
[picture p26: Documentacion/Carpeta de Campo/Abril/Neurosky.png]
    
\end{figure}

Desarrollamos la página del proyecto, creamos el GitHub donde estará todo tipo de documento y código relacionado al proyecto y una cuenta de TikTok.

\begin{figure}[H]
    \centering
    
\end{figure}

Seguimos con la programación del Neurosky Mobile Mindwave 2, además de crear publicaciones para difundirnos por Instagram.

\begin{figure}[H]
    \centering
    
\end{figure}

\newpage

\begin{center}
    \section{Mayo de 2024}
\end{center}

Probamos conectar el Neurosky con Arduino pero sigue sin funcionar. Por eso buscamos otras alternativas para el EEG, ya que debido a los intentos reiterados no funciona.

\begin{figure}[H]
    \centering
    
\end{figure}

Se investiga el driver si puede funcionar y si es viable utilizarlo o hacer el propio.

\begin{figure}[H]
    \centering
    
\end{figure}

\newpage

Fuimos a la radio en Solano a hablar del proyecto. Nos contactamos con la radio FM Sur.

\begin{figure}[H]
    \centering
    
\end{figure}

Probamos el driver y el motor originales que venían con la silla de ruedas. Se realiza un informe sobre el Driver ya que el mismo no funciona.

\begin{figure}[H]
    \centering
    
\end{figure}

Se realizó el plano de la silla de ruedas en Autocad. Se busca la forma de diseño del Driver. Nos contactamos con sponsors para darnos difusión. Organizamos el Trello.

\begin{figure}[H]
    \centering
    
\end{figure}

\newpage

Tuvimos la entrevista radial en FM Sur. Se realiza el reel n.° 3. Se continúa con el plano de la silla. Se organiza el Github. Se buscan alternativas al Neurosky. 

\begin{figure}[H]
    \centering
    
\end{figure}

Se realiza el diseño del driver para el motor. Finalmente se toma el Open BCI como alternativa para realizarla por nosotros mismos debido a los costes de fabricación. Para eso se busca la documentación.

\begin{figure}[H]
    \centering
    
\end{figure}

\newpage

Nos contactamos con ALAPA, con la Fundación Esteban Bullrich y con la política María Sotolano. Vemos la alternativa del Open BCI

\begin{figure}[H]
    \centering
    
\end{figure}

Realizamos una entrevista para que Clarín haga una nota sobre nosotros.

\begin{figure}[H]
    \centering
    
\end{figure}

Buscamos de un EEG de reemplazo que tenga un coste aceptable. Elegimos entre el Open BCI y otro circuito. Tomamos el ejemplo de la página siguiente: 

\begin{center}
    \href{https://www.instructables.com/DIY-EEG-and-ECG-Circuit/}{https://www.instructables.com/DIY-EEG-and-ECG-Circuit}
\end{center}

\begin{figure}[H]
    \centering
    
\end{figure}

\newpage

Fuimos al Congreso a hablar con la diputada María Sotolano. Logramos asegurar el contacto con la asociación Esteban Bullrich.

\begin{figure}[H]
    \centering
    
\end{figure}

TN nos entrevista, por lo que preparamos un stand para presentar en la televisión.

\begin{figure}[H]
    \centering
    
\end{figure}

\newpage

\begin{center}
    \section{Junio de 2024}
\end{center}

Damos entrevista con Radio Nacional. Se comunica con nosotros TV pública y Radio Halley. Se hace diseño en KiCad del EEG. Se empieza a programar EEG mediante transformada de Fourier. Luego se filtra la señal y se discrimina por tipo de frecuencia. Se consigue joystick del motor.

\begin{figure}[H]
    \centering
    
\end{figure}

\newpage

Se dio una entrevista en Radio Eco. Nos contactó la Radio de la Jauretche. Se optimiza el código y se lo hace aplicando transformada de Fourier inversa. Se prueba el motor y no funciona. Se empieza a programar en la Raspberry Pi 4 con respecto a los motores.

\begin{figure}[H]
    \centering
    
\end{figure}

También se dio una entrevista en Radio Halley. Se armó el tríptico, textos para imprimir y las presentaciones para el Stand en la Técnica 3 de Solano. Se desestima el ADC 1115 para utilizar la Raspberry Pi Pico mini, ya que tiene una mayor frecuencia de switcheo. Se empieza a armar el código de la Inteligencia Artificial y se arma el código de I2C para conectar la Raspberry Pi Pico con la Pi 4. Luego se programa a la Raspberry Pi Pico para utilizar su ADC.

\begin{figure}[H]
    \centering
    
\end{figure}

\newpage

Fuimos a la muestra de la Técnica 7 de Solano y se arma el Stand. Se sigue el código de I2C y ADC.

\begin{figure}[H]
    \centering
    
\end{figure}

Se realiza videollamada con CILSA y se realiza nota con TV pública.

\begin{figure}[H]
    \centering
    
\end{figure}

Se prueban los motores Arduino con la Raspberry Pi 4 para el sistema de emergencia.

\begin{figure}[H]
    \centering
    
\end{figure}

Avances en el código para la realización de modelo de predicción. Se conectan los códigos para recepción de EEG en tiempo real. Se prueba el motor, se verifica que está quemado y se verifica la funcionalidad.

\begin{figure}[H]
    \centering
    
\end{figure}

Simulación de circuito EEG y código para el filtrado digital. Se empieza a realizar la carpeta de campo. Búsqueda de puentes H y módulo PWM. Refactorización de códigos EEG. Prueba de motor.

\begin{figure}[H]
    \centering
    
\end{figure}

Se soldó un potenciómetro al motor para luego probarlo. Se revisan los códigos de IA. Se saca la silla con dos motores para probarla.

\begin{figure}[H]
    \centering
    
\end{figure}

\newpage

Se empieza a hacer funcionar al motor. El driver aun no funciona pero se detectó un código de estado del error. También se verifica el estado del freno de mano, el cual está cortocircuitado lo que produjo olor a quemado.

\begin{figure}[H]
    \centering
    
\end{figure}

Se debuggea el código de filtrado.

\begin{figure}[H]
    \centering
    
\end{figure}

\newpage

Avances en el debugging de extraction.py debido a inteligencia artificial utilizando datasets de la web. Descubrimos que lo más probable de hacer es realizar un dataset propio.

\begin{figure}[H]
    \centering
    
\end{figure}

Búsqueda de modelos de puente H. Simulación de filtrado de circuitos y rediseño de los filtros. Se empieza a realizar el diseño de KiCad. 

\begin{figure}[H]
    \centering
    
\end{figure}

\newpage

Llegan algunos materiales de cooperadora y continuamos el diseño en Kicad. Se intenta probar la recepción por medio de I2C y la Raspberry Pi Pico con la Pi 4

\begin{figure}[H]
    \centering
    
\end{figure}

En el día de la fecha se ordenaron los materiales ordenados por cooperadora y se pidieron aquellos faltantes en el pañol y lo que no había se agregó a la lista de compra. También hicimos pruebas con los motores y logramos hacerlos funcionar, además de ponerlos en condiciones para su uso. Recibimos los electrodos del proyecto Brainstream del año pasado.

\begin{figure}[H]
    \centering
    
\end{figure}

\newpage

\begin{center}
    \section{Julio de 2024}
\end{center}
Se empieza a realizar el circuito en el PCB. Se empieza a debuggear el código de recepción, aunque aún con inconvenientes en la conexión.

\begin{figure}[H]
    \centering
    
\end{figure}

Se encuentra un Puente H que supuestamente aguanta hasta 48 A. Se finaliza el pcb del circuito EEG. Se establece la conexión I2C entre los micros. Se prueba el circuito de filtro pasabajos. Se busca alternativa al Driver Arduino por transistores que aguanten la corriente y hacerlo por nosotros mismos. 

\begin{figure}[H]
    \centering
    
\end{figure}

\newpage
Se realiza la conexión I2C entre la Pi 4 y la Pi Pico. Se van refactorizando los códigos y mejorando el rendimiento de la conexión para mejorar la rapidez. Por otro lado, ya se hizo el pedido de los transistores Mosfet que soporten la corriente de 24 A para realizar el puente H.

\begin{figure}[H]
    \centering
    
\end{figure}
Se comenzó a realizar la carpeta técnica, tanto en word como en LaTeX. Conexión entre i2c y los microcontroladores, mejorando la velocidad para las mediciones y refactorizando el código. Creación de modelo 3D del PCB y finalización del EEG. Realización de puente H por señales PWM.

\begin{figure}[H]
    \centering
    
\end{figure}

\newpage
Se empieza a hacer una placa modelo para el EEG la cual luego se enviará a China para la posterior confección. Se sigue intentando con la conexión i2c, primero probándola en una Pico sola y luego la comunicación entre micros; sin embargo, siguen habiendo errores y retrasos.

\begin{figure}[H]
    \centering
    
\end{figure}

Se modifica el protocolo a utilizar de i2c a UART debido a una mayor simplicidad en la comunicación y menos problemas. Además, por otra parte se investigan los disipadores a utilizar en el puente H. Se confecciona finalmente el sistema de emergencia para realizar el PCB. Se descubre que se puede simular PWM por software.

\begin{figure}[H]
    \centering
    
\end{figure}

\newpage

\begin{center}
    \section{Agosto de 2024}
\end{center}

Se comienza a realizar el codigo para mover los motores mediante PWM. Se toma las medidas del craneo de Nicolas Fabian Adell para crear la vincha/casco para colocar los electrodos. Se soluciona el problema del refresco de las muestras. Se sigue realizando la carpeta tecnica. Se comenzo a grabar un video para reels. 

\begin{figure}[H]
    \centering
    
\end{figure}

\begin{figure}[H]
    \centering
    
\end{figure}

\newpage
Se empieza a corregir los otros códigos para adaptar esta nueva forma de lectura al resto de código. Se usa un template en LaTex para la documentación.

\begin{figure}[H]
    \centering
    
\end{figure}

Se trabaja con los códigos de recepción y se empieza a modificar el circuito de filtro. Se sube reel a instagram. Se modifica el código para graficar.

\begin{figure}[H]
    \centering
    
\end{figure}

\newpage
Se hace el código de PWM y se añaden dos filtros nuevos para el código de filtrado digital (filtro FIR y filtro IIR). Se comienza a mejorar la IA. Se mejora el pcb del puente H. Se simula circuito de offset.

\begin{figure}[H]
    \centering
    
\end{figure}

Investigación de combinación de las señales en el EEG. Soldado de componentes placa de sistema de emergencia y filtro EEG. Se unen los códigos del Puente H y del main del sistema de emergencia. Se encuentran las formas de combinar las señales de los canales en el EEG. Se sigue realizando la carpeta técnica. Se arma el programa app.py el cual va a ser el encargado de conectar todos los códigos. En el mismo ya se implementaron la recepción constante y el procesamiento aplicado con filtros.

\begin{figure}[H]
    \centering
    
\end{figure}

\newpage
Se decide organizar el código en programación orientada a objetos para, de esta manera, tener una mejor organización. De esta manera, se crean clases tales como DspBias, Bias, ReceptionBias y ProcessingBias, FilterBias.

\begin{figure}[H]
    \centering
    
\end{figure}

Estuvimos en la feria regional de la UNQ. Se crea clase graphing y se termina diseño de la placa con la RP2040 Zero. 

Se crea la clase BiasAI para empezar a codificar. Se adapta el código para que exista un PWM invertido. Se averigua para comprar los AD620AN. Se diseña la unión de las tres partes del circuito para evitar que se filtre ruido y pueda afectar el desempeño de la Pi 4. De esta forma, se tienen dos masas distintas en todo el circuito.

\begin{figure}[H]
    \centering
    
\end{figure}

Se prueban el código de los motores. Se sueldan los componentes de los circuitos de EEG y del sistema de emergencia. Se arreglan los errores del código de Emergencia.

Se termina de soldar los componentes de los circuitos. Se decide como hacer la estructura del EEG. Se sigue desarrollando la estructura de la silla. Se investiga sobre las jaulas de Faraday. Se codifica la clase BiasAI. 

Se obtiene el dinero para comprar amplificadores AD620AN. Se siguen soldando las plaquetas para luego leer señales cerebrales.

\newpage

\begin{center}
    \section{Septiembre de 2024}
\end{center}

Se trabaja con la extracción de features para el entrenamiento de la IA, utilizando señales sintetizadas. Se intenta lograr que tengan las mismas dimensiones que la capa de entrada. Se diseña el circuito de alimentaciones para la Pi 4 (etapa de control).

\begin{figure}[H]
    \centering
    
\end{figure}

Se trabaja con los modelos de inteligencia artificial, viendo que ya se puede entrenar y va prediciendo comandos. El modelo utiliza una red neuronal convolucional.

\begin{figure}[H]
    \centering
    
\end{figure}

\newpage
Se sigue realizando la carpeta técnica. Se suelda el primer canal del EEG. Se investiga sobre el multiprocessing y el multithreading con python. Se realizan códigos para el multithreading. Se mide la señal de la salida de la placa de los filtros. Se prueba la corriente del motor para calcular las dimensiones de los capacitores.

\begin{figure}[H]
    \centering
    
\end{figure}

Probamos el circuito de filtrado y se encontró un problema. El último notch tenía las entradas inversoras y no inversoras invertidas

\begin{figure}[H]
    \centering
    
\end{figure}

Probamos el circuito de filtrado y se soluciono el problema que encontramos el día anterior. Probamos el circuito de emergencia desde el PCB. Se sigue realizando la carpeta técnica. Se encuentra un error en la última etapa de notch, que por alguna razón empieza a amplificar luego de los 100 Hz.

Se avanza con el soldado de la placa de offset. A su vez se termina el diseño del puente H para imprimir y finalmente se descarga el dataset BCI IV 2a. para luego utilizarlo para el entrenamiento del modelo.

\begin{figure}[H]
    \centering
    
\end{figure}

Se programa un Arduino Nano 3.0 para usar un joystick y mover los motores. Por lo tanto, se crea un programa de slave para la arduino y un programa de master para la Raspberry Pi 4.

\begin{figure}[H]
    \centering
    
\end{figure}

\newpage
Se prueba la placa de emergencia, se ve que hay un error en el buzzer y posteriormente se termina la placa de alimentación para la Pi 4. Se termina de realizar la lista para la compra de materiales. Se descubre que la plaqueta de alimentación contiene el LED rojo al revés. Se terminan de planchar las pistas del puente H y se estañan las mismas.

\begin{figure}[H]
    \centering
    
\end{figure}

Se prueba el circuito de offset y se descubre que el diodo Zener práctico no es igual a la simulación ya que en el mismo circula corriente aunque sea menor a la tensión esperada. Se prueba circuito de transmisión por UART y se ve que a la salida no le llega nada a la Pi 4. Se descubre que el problema en la plaqueta de la comunicación UART es la velocidad de transmisión. Se puede transmitir hasta 9600 baudios. Por esa razón, se reemplaza por un optoacoplador 6n137 y por un transistor 2n2222.

\begin{figure}[H]
    \centering
    
\end{figure}

Se va a hablar con una técnica neuróloga en el hospital del cruce con el objetivo de que nos muestre las instalaciones EEG y nos despeje algunas dudas de la localización de los electrodos..

Se van a comprar los componentes restantes y se resuelve el problema de la velocidad de comunicación UART mediante el reemplazo de los materiales nombrados anteriormente. Se rediseñan las placas por tema de alimentaciones y, por último, se rediseña la placa de recepción. Además, se sueldan los últimos componentes del puente H. Por otro lado, se piensa en hacer una silla de diseño 3D chiquita.

Se prueba el puente H y nos damos cuenta de un error, y es que circulan 160 A cuando ambas entradas PWM están en cero. Se prueba el circuito de filtrado en protoboard pero termina un AD620AN quemado debido a que las alimentaciones estaban invertidas. Por otro lado, se realiza la plaqueta de control de la Pi 4.

\begin{figure}[H]
    \centering
    
\end{figure}

\newpage
Se arreglan ciertas incoherencias en la “shape” del dataset del código de la IA. Se realiza el banner y se manda a cooperadora.

\begin{figure}[H]
    \centering
    
\end{figure}

Se prueba el circuito de filtrado sin el último filtro Notch. Este último distorsionaba la señal al punto de aumentarla hasta los 120 Hz y disminuye luego de esta frecuencia. Sin este último nos aseguramos que no haya distorsión. Se termina de soldar el circuito de control y recepción de datos. Se prueba el circuito de offset y nos damos cuenta que el zener empieza a conducir antes de que la señal se recorte, por lo que sugerimos cambiar la resistencia. De esta forma, la tensión de la resistencia será menor.

\newpage

\begin{center}
    \section{Octubre de 2024}
\end{center}

Se comienza a diseñar la jaula de Faraday. Se miden los PCBs. La silla de madera termina de ser fabricada.

\begin{figure}[H]
    \centering
    
\end{figure}

Se comienza a realizar el Informe Técnico del proyecto para presentar en las ONIET.

\begin{figure}[H]
    \centering
    
\end{figure}

\newpage

Se probó el circuito de filtrado con los electrodos, usando la cabeza de Santiago Sojka. Se sigue realizando la carpeta técnica. Se buscan soluciones a los errores del puente H.

\begin{figure}[H]
    \centering
    
\end{figure}

Se prueba nuevamente la placa de filtrado con osciloscopio digital. Se prepara todo para entregar el informe descriptivo y el informe de redes sociales para las ONIET.

Se diseña un nuevo circuito de puente H que tiene más probabilidades de funcionar. Se termina y luego se refactoriza el programa que permite entrenar al algoritmo de machine learning.

Se hace funcionar el puente H con un nuevo circuito. En este caso, lo que hicimos fue hacer un cruce entre los gates de los mosfets y, de esta forma, vimos que la carga podía tener +24 V, -24 V y 0 V. Por último, se intentó probar todas las etapas de filtros y nos dimos cuenta que las baterías estaban descargadas.

\newpage

Se prueban todas las placas juntas y nos damos cuenta que hay un error en una plaqueta debido a que había una pata de resistencia haciendo cortocircuito con masa. Después, se empieza a hacer la jaula de Faraday de madera. Por último, se terminan todas las placas de filtros y se empiezan a probarlas. Se prueban todas las placas juntas para ver la gráfica de señales en la terminal con los 9 electrodos juntos.

\begin{figure}[H]
    \centering
    
\end{figure}

\begin{figure}[H]
    \centering
    
\end{figure}

Se termina de realizar la placa del puente H. Se empieza a diagramar las conexiones. Se avanza en realizar la carpeta técnica. Se ve que el modelo de inteligencia artificial posee un 25\% de precisión.

\begin{figure}[H]
    \centering
    
\end{figure}

Lo siguiente que hicimos fue probar el puente H con un motor de poco consumo. Se prueba el modelo con SVM y CSP para ver cómo se comportan antes las señales. Se modifican las dimensiones de las señales y de las features para poder entrenarlas.

Lo que se prueba en este día es la utilización del filtrado PCA para ver el comportamiento de la IA.

Se prepara todo para llevar a Córdoba. Se piden los materiales necesarios para llevar. Se prueba todo en conjunto y el puente H se quema por errores de código y zeners ya quemados. Se imprime la documentación para llevar. En este mismo día volvimos a reconstruir el puente H

\newpage

Se viaja a Córdoba a competir. Competimos en prototipos y ganamos medalla de oro. Ademas, competimos en innovation teams y feed de instagram. El dia de la competencia resultó que los mosfets estaban quemados.

\begin{figure}[H]
    \centering
    
\end{figure}

En las competencias se nos quemó un puente H, por lo que realizamos pruebas de los motores para ver si seguían en buen estado

\begin{figure}[H]
    \centering
    
\end{figure}

\newpage

Encontramos nuevos mosfets para probar el puente H. Se intenta reconstruir. Se empieza a programar el dataset con college; sin embargo, nos damos cuenta que tambien existen otros modelos.

El día de hoy se prueba el puente H con una fuente y termina uno quemado. Luego, probamos el que modificamos y terminó funcionando. Además, se hace el cableado de los ultrasonidos. Conseguimos un 50 \% de precisión con el modelo EEGNet.

Se consigue un 64\% de precisión en la inteligencia artificial. Se diseña el cableado general de la silla

Se consigue gabinete para la jaula de Faraday y se imprime gabinete en 3D para el puente H. Se compra transistor canal P que se había quemado Se adapta el dataset a diferencias de potencial en vez de la referencia a masa.

Se prueban los electrodos junto a la IA para ver que se predice, midiendo la cabeza del sujeto que lo prueba. Sin embargo, en el hangar había demasiado ruido electromagnético.

\section{Noviembre de 2024}
Se prueba entrenar la IA con ruido, estandarizarla y probar con distintas bandas de frecuencia. Se le agregan switches a los sistemas

Se prepara la jaula para poder juntarla con las placas. Se suma un capacitor en paralelo a las placas para correr el filtro notch a 50 Hz. Se ensamblan los puentes H a la estructura

Se entrenan los modelos con datos personalizados. Se ensamblan las cosas para juntarlas en la jaula de Faraday. Se ponen los mallados para pasar los electrodos. Se pasan los cables por termocontraíbles.

Se expone el proyecto en la feria de ciencias.

\end{document}

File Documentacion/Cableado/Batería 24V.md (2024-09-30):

Salida:
[[Puente H]]
[[Placa reguladora 24V-15V]]
[[Placa Reguladora 24V-15V-5V]]

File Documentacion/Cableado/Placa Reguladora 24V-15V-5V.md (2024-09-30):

Entrada:
[[Batería 24V]]
Salida:
[[Raspberry Pi 4]]

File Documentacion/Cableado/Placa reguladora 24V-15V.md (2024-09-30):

Entrada:
[[Batería 24V]]
Salida:
[[Puente H]]

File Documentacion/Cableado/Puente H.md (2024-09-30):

Entrada:
[[Raspberry Pi 4]]
[[Batería 24V]]
[[Placa reguladora 24V-15V]]
Salida:
[[Motor]]

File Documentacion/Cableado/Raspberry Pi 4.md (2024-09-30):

Entrada:
[[Sistema de Recepción]]
[[Sistema de Offset]]
[[Placa Reguladora 24V-15V-5V]]
Salida:
[[Sistema de Emergencias]]
[[Puente H]]

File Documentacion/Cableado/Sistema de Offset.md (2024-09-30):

Entrada:
[[Sistema de Filtros]]
Integra:
[[Raspberry Pi Pico]]
Salida:
[[Sistema de Recepción]]
[[Raspberry Pi 4]]

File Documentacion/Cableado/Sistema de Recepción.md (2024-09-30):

Entrada:
[[Sistema de Offset]]
Salida:
[[Raspberry Pi 4]]

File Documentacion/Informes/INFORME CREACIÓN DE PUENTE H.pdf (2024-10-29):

# INFORME CREACIÓN DE PUENTE H

## Díaz Melión Danilo

## ESQUEMÁTICO FINAL


Este esquemático representa un circuito puente H para controlar la dirección y velocidad de un motor de corriente continua (DC) utilizando señales PWM (modulación por ancho de pulso) provenientes de un microcontrolador, como la Raspberry Pi Pico.

## FUNCIONAMIENTO GENERAL

El circuito mostrado utiliza dos señales PWM (PWM1 y PWM2) para controlar la rotación de un motor de corriente continua (DC) mediante un puente H, que está compuesto por cuatro transistores MOSFET (Q1, Q2, Q3, y Q4). Este puente permite invertir la polaridad del voltaje aplicado al motor, cambiando su dirección de rotación. El control de la velocidad del motor se consigue ajustando el ciclo de trabajo (duty cycle) de las señales PWM, que modulan la potencia entregada al motor.

Descripción de los Componentes:

U1 y U2 (PC817 - Optoacopladores): Estos optoacopladores proporcionan aislamiento entre el circuito de control de baja tensión (Raspberry Pi Pico) y el circuito de potencia de alta tensión (24V). Protegen el microcontrolador de interferencias o picos de voltaje generados por el circuito de potencia. La entrada de PWM activa el LED interno del optoacoplador, que a su vez activa el fototransistor, transfiriendo la señal al lado de potencia.

Q1 y Q3 (IRF4905 - MOSFET canal P): Estos MOSFET están en la parte superior del puente H y controlan el lado positivo de la alimentación del motor. Se activan cuando la señal en su puerta está en bajo (0V), permitiendo el paso de corriente desde la fuente de 24V hacia el motor.

Q2 y Q4 (IRF2805 - MOSFET canal N): Ubicados en la parte inferior del puente H, estos MOSFET conectan el motor a tierra cuando están activados. Se activan cuando la señal PWM en su puerta es alta (5V), cerrando el circuito y permitiendo que el motor gire en la dirección deseada.

D1, D2, D3, y D4 (Diodos Zener 1N4742A): Los diodos Zener están conectados en paralelo a cada MOSFET para protegerlos contra picos de voltaje inducidos por la conmutación del motor, especialmente cuando el motor cambia de dirección o se apaga abruptamente. Además, limitan el Vgs a 12V, lo cual lo sitúa por debajo de la línea máxima de ±20V la cual quemaría los Zener.

R1 y R2 (Resistencias de 47 ohms): Estas resistencias limitan la corriente de entrada a los LEDs internos de los optoacopladores U1 y U2, evitando daños debido a sobrecorriente. Su bajo valor se debe a que es el necesario para el correcto funcionamiento de la placa Raspberry Pi 4.

R3, R4, R5, R6, R7, y R8 (Resistencias de 680 ohms y 2.7k): Las resistencias R3, R5, y R6 limitan la corriente de las compuertas de los MOSFET de canal N (Q2 y Q4), asegurando un control estable de su activación.
Las resistencias R4, R7, y R8 hacen lo mismo para los MOSFET de canal P (Q1 y Q3), ayudando a desactivar los MOSFET rápidamente cuando la señal PWM deja de estar presente.

Conectores PWM (J1 y J2): Estos conectores reciben las señales PWM del controlador (por ejemplo, Raspberry Pi Pico), que determinan la velocidad y dirección del motor.

Conector de alimentación (J3): Proporciona la alimentación de 24V necesaria para el funcionamiento del motor y de los MOSFET en el puente H.

SW1 (Interruptor): Este interruptor conecta o desconecta el circuito del lado de la tierra, permitiendo activar o desactivar todo el sistema.

## SELECCIÓN DE MOSFETS

En los trabajos de ingeniería, especialmente en aplicaciones de potencia, se suelen usar MOSFETs con características similares para garantizar consistencia, eficiencia y compatibilidad en los circuitos. Esto facilita el diseño y la fabricación, ya que los ingenieros pueden optimizar las soluciones de manera más predecible, minimizando variaciones en el rendimiento. Además, permite una mejor gestión térmica y evita problemas de integración que podrían surgir con componentes desiguales, asegurando una mayor confiabilidad. Dicho esto, para este proyecto elegí los MOSFETs IRF2805 e IRF4905, con las siguientes características:

IRF4905 (P-Channel MOSFET): Tipo: Canal P
Tensión de drenaje-fuente (Vds): -55V
Corriente de drenaje (Id): -74A
Resistencia en estado de encendido (Rds(on)): 0.02Ω Voltaje de compuerta-fuente (Vgs): +/- 20V
Tipo de encapsulado: TO-220

IRF2805 (N-Channel MOSFET):

Tipo: Canal N
Tensión de drenaje-fuente (Vds): 55V
Corriente de drenaje (Id): 82A
Resistencia en estado de encendido (Rds(on)): 0.0045Ω Voltaje de compuerta-fuente (Vgs): +/- 20V
Tipo de encapsulado: TO-220

ACTUALIZACIÓN: En el proceso se tuvo que cambiar el IRF2805 por el IRF3205, del cual adjunto información acá:

- Voltaje de drenaje-fuente (Vds): 55V
- Corriente de drenaje continua (Id): 110A
- Resistencia de encendido (Rds(on)): 0.020Ω (máx.)
- Voltaje de compuerta-fuente (Vgs): +/- 20V
- Tipo de encapsulado: TO-220

## SELECCIÓN DE BORNERAS

La selección de borneras garantiza la conexión segura y eficiente de los cables dentro de un circuito. Las borneras permiten una conexión fácil, facilitando el mantenimiento, la expansión y la modificación de los sistemas.
Para elegir las borneras adecuadas, se deben considerar factores como la corriente y voltaje del cable a usar y el tipo de cableado, entre otras cosas. Una correcta selección optimiza el rendimiento del sistema y minimiza riesgos de fallos eléctricos.


Optamos por utilizar las borneras DT-69-B01W-02 debido a que su paso de 11mm permite acomodar cómodamente los cables requeridos para manejar corrientes de hasta 30A. Este tamaño es suficiente para garantizar una conexión segura.
En cuanto a la parte de control, hemos preferido utilizar pines genéricos, ya que la demanda de potencia en esa sección es baja y no representa un desafío que justifique el uso de conexiones especializadas.

## SELECCIÓN DE CABLES

Para este propósito, es necesario consultar las reglas AWG para seleccionar el diámetro de la sección en mm² según el amperaje que debe soportar. A continuación, adjuntamos la tabla correspondiente.


Dado que la potencia máxima del motor es de 500W y que opera a 24V, se estima que la corriente máxima será de aproximadamente 23,95A. Por esta razón, se ha decidido utilizar cables con una sección de 6 mm², lo cual asegura un rendimiento adecuado y seguro en las condiciones previstas de operación.

## SELECCIÓN DE DISIPADORES

La selección de disipadores adecuados para un puente H de potencia es crucial para garantizar una correcta gestión térmica y evitar el sobrecalentamiento de los MOSFETs o transistores involucrados. Un diseño óptimo de disipación asegura que el puente H opere dentro de los rangos de temperatura seguros, lo que mejora la eficiencia y prolonga la vida útil del sistema. Por esto mismo, se han realizado cálculos de potencia disipada por los transistores en la condición que más potencia les exige, todo con el objetivo de lograr que el disipador sea adecuado en todas las condiciones de trabajo en las que se exponga al MOSFET. Los cálculos son presentados a continuación:

IRF4905


IRF2805


Los cálculos fueron realizados siempre tomando como referencia las condiciones de más consumo.
Por ambos cálculos, se ha determinado que una resistencia térmica de 15°C/W es adecuada para asegurar un correcto rendimiento térmico de los transistores. En función de esta información, se seleccionaron los disipadores D-5225D2.


}

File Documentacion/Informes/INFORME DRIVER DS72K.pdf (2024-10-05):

# INFORME DRIVER DS72K

Díaz Melión Danilo. 7°2 Aviónica “C”


En este informe se detalla el procedimiento utilizado y la conclusión final acerca del uso de este driver para movilizar una silla de ruedas eléctrica.

Es de extrema importancia aclarar que la silla de ruedas, como fue encontrada, carece del joystick capaz de mover el motor y accionar la silla, por lo cual se buscó analizar su funcionamiento para encontrar una alternativa a la unidad de mando faltante.

# PROCEDIMIENTO

Primero, se optó por abrir el driver para intentar descubrir su funcionamiento mediante el PCB interno.


Imagen 1: El driver DS72K por dentro

A partir del seguimiento del circuito, se pudo deducir la lógica de funcionamiento del control de mando. Además, mediante el uso de la manual de usuario y el manual de service de la silla de ruedas, se pudieron realizar los siguientes gráficos:


Imagen 2: Funcionamiento interno del potenciómetro dentro del PCB y conexiones entre Conector de control y el conector que correspondería al joystick.

Imagen 3: Gráfico de puente H usado por el driver y el Conector del Motor.

Se pudieron sacar algunas importantes observaciones:

Imagen 2:
- Abajo a la izquierda está el conector del driver (8 pines) y a su derecha el otro conector, al que le “faltan pines”, pero no falta nada, esos pines faltantes son para funciones que este modelo en particular no presenta.
- Siempre hay que calibrar el potenciómetro en caso de un servicio para definir el punto medio que es la posición de neutral (en reposo, no avanza ni retrocede).
- En el caso del potenciómetro, del punto medio a cada extremo se controlan 2 volt (0,5V; 2,5V; 4,5V). Lo que hace el potenciómetro es modificar las tensiones de esos pines.
- El potenciómetro se ataca a los operacionales que actúan como comparadores de tensión, con una resistencia de 22k en cada pin, asegurando fallos o conexiones erróneas.

Imagen 3:
- Abajo a la izquierda, están los pines del motor y solenoide de estacionamiento, el solenoide es controlado por un FET BSP78 que energiza la bobina.
- A la derecha se ve el puente H que controla el motor.

Todo esto especificado en las páginas del manual de usuario e incluso el de service.

Luego, se elaboró una posible idea para montar el potenciómetro y probar el driver/motor, la cual adjunto acá:


# PRIMERA CONCLUSIÓN

Estamos ante un joystick que funciona analógicamente, el potenciómetro de este haría que se genere una variación en tensión desde el punto medio y eso generaría el movimiento. Y siguiendo la naturaleza de los joysticks, al estar en reposo este vuelve al centro en caso de no aplicarle fuerza externa, por lo cual en ese punto no habría movimiento ya que no hay variación.

Luego de esta conclusión, se investigó acerca de sillas de ruedas marca Merits y cuales son los sistemas de movimiento de estas, también a buscar cuales joysticks utiliza.
Ahí es donde surgió el primer potencial inconveniente:

“Lo que saco en limpio es que podremos ver si el motor funciona o no pero no sé si tendremos control del mismo. el Joystick tiene mucho más que un potenciómetro”

Luego, se observó por dentro cómo está constituido un mando de Merits regularmente:


Imagen 4: Joystick de silla de ruedas Merits.

Esto plantea la primera falla para utilizar el motor, ya que si realmente se moviera con el pote, se podría diseñar un control simulando el pote en reemplazo del joystick, pero se observa que tiene mucha lógica adentro, muy difícil de realizar por propia cuenta en caso de la ausencia del joystick que afrontamos.

Sin embargo, se procedió a darle alimentación (24V) y ver si gira en uno u otro sentido, junto con la conexión del solenoide.

El procedimiento se llevó a cabo, y se intentó controlar con el módulo de joystick KY-023. Adjunto evidencia del hecho:


Imagen 5: Prueba del motor y solenoide interno.
El resultado fue claro: El motor no emitió movimiento alguno.

# CONCLUSIONES

Ante la prueba del motor, es evidente denotar que el resultado debería haber sido el movimiento de las ruedas, pero como se puede evidenciar, ese no ha sido el caso. En base a la investigación, pruebas y análisis que se llevaron a cabo, podemos sacar las siguientes conclusiones:

- El motor no se mueve mediante la diferencia de tensión generada por el potenciómetro. Es decir, el potenciómetro no es el generador de movimiento y el movimiento no se genera analógicamente.
- Dentro de la prueba del motor, se midió cada una de las patas del potenciómetro, donde se concluye que existe una falla en el driver que impide que llegue correctamente la tensión.
- El motor funciona digitalmente en un procedimiento similar al PWM. El potenciómetro se encarga de variar los pulsos que llegan para que un microcontrolador se encargue de generar el movimiento.

Por lo tanto, si no podemos acceder al joystick original que venía junto al motor/driver y la silla de ruedas, ni nosotros ni cualquier persona interesada en ocupar esto podrá hacer mucho a no ser que recupere la pieza faltante. Este hecho debería ser marcado para así quienes decidan utilizarlo en un futuro tengan en cuenta aquello que nosotros no pudimos considerar ya que no teníamos conocimiento de esta problemática.

—--------------------------------------------------------------------------------------------------------------------

# INVESTIGACIÓN

Se adjuntan algunos links utilizados en la investigación:

https://www.youtube.com/watch?v=DVUY54e-wRI&ab_channel=dru idalocobrokel (https://www.youtube.com/watch?v=DVUY54e-wRI&ab_channel=druidalocobrokel)

https://www.youtube.com/watch?v=Qg9tJg-VlLc&t=145s&ab_channel=AlbertoMatilla (https://www.youtube.com/watch?v=Qg9tJg-VlLc&t=145s&ab_channel=AlbertoMatilla)

https://www.youtube.com/watch?v=6gCPKZ9ttSA&ab_channel=AO LElectrónica (https://www.youtube.com/watch?v=6gCPKZ9ttSA&ab_channel=AOLElectr%C3%B3nica)

https://www.meritshealth.com/power-wheelchairs

https://www.meritshealth.com/power-wheelchairs/folding/p113-yoyo

https://www.ebay.com/sch/i.html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 (https://www.ebay.com/sch/i.html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)

https://www.medicalexpo.es/prod/merits-health-products/product-76 814-657796.html (https://www.medicalexpo.es/prod/merits-health-products/product-76814-657796.html)

Además, se adjuntan hojas de apuntes sobre los cuales se realizó el análisis del circuito:




Además se utilizaron 3 PDF´s que son los siguientes:

- Manual de Instalación de RHINO70 (familia DS70K)
- Manual de Usuario DS72K y similares
- Manual de Service DS72K y similares

## ESTIMACIÓN DE TIEMPO UTILIZADO EN LA REALIZACIÓN DE ESTE INFORME: 15 HORAS

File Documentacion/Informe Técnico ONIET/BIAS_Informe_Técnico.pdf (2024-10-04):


Integrantes del Proyecto:

Adell, Nicolas Fabian (DNI 47020472)

De Blasi, Luca (DNI 47382528)

Diaz Melion, Danilo Sebastian (DNI 47307165)

Gil Soria, Ian Lucas (DNI 47337154)

Montenegro, Luciano Nahuel (DNI 47256543)

Sojka, Santiago Alejandro (DNI 47306441)


## Índice

1. Introducción | 3
2. ¿Quiénes somos? | 3
3. ¿Por qué hacemos este proyecto? | 3
4. ¿A quiénes está dirigido este proyecto? | 3

1

5. ¿Por qué es innovador este proyecto? | 4
6. Descripción física del proyecto | 4
7. Investigaciones realizadas | 5
8. Descripción del funcionamiento | 6
9. Desarrollo Técnico | 8
10.Circuitos usados | 11
11.Agradecimientos | 14

2

## 1. Introducción

El proyecto BIAS es un módulo diseñado para su aplicación en sillas de ruedas, permitiendo al usuario dirigirla mediante el control mental, es decir, a través de sus pensamientos. Con este enfoque, se elimina la necesidad de utilizar un control físico, como el joystick empleado en las sillas eléctricas convencionales. De esta manera, se ofrece mayor independencia y una mejor calidad de vida a personas con movilidad reducida, como aquellos que padecen esclerosis lateral amiotrófica (ELA).
Para su funcionamiento, BIAS emplea una Inteligencia Artificial desarrollada por nuestro equipo, capaz de reconocer los patrones de las señales cerebrales asociadas al movimiento. Estos patrones se traducen en acciones que permiten dirigir la silla en distintas direcciones o, si el usuario así lo desea, mantenerla en su posición actual.

## 2. ¿Quiénes somos?

El equipo BIAS (Brain Intelligence Artificial System) está conformado por seis integrantes, todos estudiantes de la Escuela Técnica N° 7 ÏMPA"de Quilmes. Actualmente, nos encontramos cursando el séptimo y último año de la educación secundaria, en la especialidad de Aviónica, más específicamente a la segunda división, comisión Ç".

### 2.1. Metodología de Trabajo

La metodología aplicada en este proyecto se basa en la organización del equipo en dos grupos especializados. El primer grupo se encarga del desarrollo de los programas, siendo ejemplos de esto los filtros virtuales, programas de recepción y procesado, mientras que el segundo se dedica a la implementación de los motores, sistemas de emergencia y filtros. Esta división del trabajo permite una utilización más eficiente del tiempo, al abordar simultáneamente diversas áreas del proyecto, lo que resulta en un avance más significativo en periodos de tiempo más reducidos.
Dedicamos aproximadamente 30 horas semanales, durante 28 semanas, al desarrollo del proyecto desde principios de marzo, en el contexto de la asignatura "Prácticas Profesionalizantes". Durante este período, todo el tiempo asignado a dicha materia se ha destinado exclusivamente a la planificación, investigación y ejecución de las diferentes etapas del proyecto. En dicha materia, tenemos a cargo a tres profesores, quienes son:

Fabrizio Carlassara

Sergio Medina

Carlos Bianco

## 3. ¿Por qué hacemos este proyecto?

Como estudiantes de séptimo año, nuestro objetivo es desarrollar un proyecto que cumpla con los requisitos de las prácticas profesionalizantes. Desde un principio, nos propusimos encontrar una iniciativa que generara un impacto social significativo, centrada en mejorar la calidad de vida de personas con discapacidades. En este contexto, y luego de investigar, pensamos en la idea de crear un módulo para sillas de ruedas controlado por la actividad cerebral del usuario, utilizando tecnología de interfaz cerebro-computadora (BCI).

## 4. ¿A quiénes está dirigido este proyecto?

Este proyecto está dirigido a personas con movilidad reducida, especialmente aquellos pacientes que presentan una parálisis completa desde el cuello hacia abajo. Entre los principales beneficiarios se encuentran personas que padecen esclerosis lateral amiotrófica (ELA), cuadriplejia, esclerosis

3

múltiple, o aquellos que han sufrido la amputación de extremidades. Dado que el control de la silla de ruedas se realiza a través de señales cerebrales, el alcance del proyecto puede extenderse a una amplia variedad de pacientes con limitaciones motrices de este tipo.
Estamos convencidos de que este proyecto tiene el potencial de transformar la vida de personas con movilidad reducida, permitiéndoles gestionar su propio movimiento y mejorando sustancialmente su calidad de vida, y puede llegar a tener un alcance incluso mundial si es comercializado correctamente.

## 5. ¿Por qué es innovador este proyecto?

Consideramos que este proyecto es innovador debido a la escasez de opciones similares en el mercado, sumado a nuestro enfoque en hacerlo accesible para el mayor número posible de personas, facilitando su adquisición por aquellos que lo necesiten. Un aspecto clave de este proyecto es la integración de inteligencia artificial en su funcionamiento, lo que lo diferencia de las soluciones convencionales. Mientras que la mayoría de las sillas de ruedas disponibles se controlan mediante un joystick, esta sería una de las primeras en emplear señales cerebrales para su operación.
La inversión en tiempo y recursos adicionales permitirá perfeccionar sus características técnicas, optimizar su funcionalidad, y adaptar el producto a las necesidades de un mercado que se expande. Una vez finalizado y refinado, el proyecto podrá captar la atención de un público más amplio, lo que incrementará su viabilidad comercial y su posicionamiento en el mercado.
En caso de que el desarrollo del proyecto no se complete en su totalidad, este podrá ser aprovechado por la institución educativa, permitiendo que otros grupos de estudiantes continúen su avance. De esta manera, el proyecto no solo servirá como un recurso valioso para futuras generaciones, sino que también fomentará la colaboración y el aprendizaje continuo dentro de la comunidad académica, garantizando su evolución y finalización.
El presente proyecto tiene como objetivo generar un impacto significativo en la sociedad, fomentando el desarrollo de tecnologías basadas en el control mediante señales cerebrales. Este enfoque tiene el potencial de ampliar las opciones tecnológicas disponibles para personas con limitaciones físicas severas, que les impiden operar dispositivos de manera manual. Con la implementación de este tipo de sistemas, se busca facilitar la creación de soluciones tecnológicas accesibles y eficientes, que permitan a los usuarios controlar una amplia gama de dispositivos mediante interfaces cerebro-computadora (BCI), mejorando así su autonomía y calidad de vida.

## 6. Descripción física del proyecto

En el estado actual del proyecto, el asiento y el motor de la silla de ruedas se encuentran separados. El asiento, fabricado en madera, tiene dimensiones de 65 cm de altura, 40 cm de ancho y 40 cm de profundidad. Por su parte, el motor tiene unas dimensiones de 40 cm de altura, 95 cm de longitud y 70 cm de ancho. Estas especificaciones corresponden a la etapa preliminar del diseño, donde se busca optimizar la integración estructural y funcional de ambos componentes, asegurando tanto la estabilidad del conjunto como su eficiencia operativa.

4


Figura 1: Asiento de la silla de ruedas


Figura 2: Motor de la silla de ruedas

## 7. Investigaciones realizadas

Para concretar la idea principal del proyecto y dar inicio a su desarrollo, se realizaron investigaciones exhaustivas en diversas áreas. Estas incluyeron el análisis de proyectos similares, como el de la silla de ruedas controlada por la mente conocida como Milo, así como estudios más específicos sobre componentes técnicos clave, tales como el puente H de potencia, los filtros, y el sistema de compensación de offset. También se llevó a cabo una investigación detallada sobre dispositivos EEG, como el NeuroSky, que inicialmente fue utilizado pero posteriormente descartado. Además, se profundizó en el estudio de las señales cerebrales y los métodos para su medición. Como parte del

5

proceso, nos contactamos con diversas fundaciones y expertos en el área, con el objetivo de obtener información adicional y recibir apoyo en la implementación del proyecto.

## 8. Descripción del funcionamiento

El usuario se sienta en la silla de ruedas y se coloca el dispositivo EEG. El EEG capta las señales cerebrales y las somete a un proceso de filtrado por hardware de varias etapas. Luego, las envía a un circuito de compensación de Offset, para que la RP2040 Zero pueda leerlas. Estos datos, se los envía a la Raspberry Pi 4, en donde está el programa principal de la silla de ruedas.
En esta placa se encuentran los filtros digitales, el programa para el control de los motores, el procesamiento de señales y la inteligencia artificial. Una vez que las señales llegan a la Raspberry Pi 4, se las filtra digitalmente para eliminar el ruido de las señales. Luego de ser filtradas, se las envía a la IA, que reconoce los patrones cerebrales, y dependiendo de a dónde se quiera mover el usuario, enviará una señal a los motores en la dirección deseada, ya sea hacia adelante, detrás, izquierda, derecha o mantenerse en el lugar.

### 8.1. Informacion Adicional

La silla desarrollada en este proyecto es un prototipo, es decir, puede contener fallas de todo tipo, y es sujeto a modificaciones a futuro. Se recomienda su uso siempre acompañado, en zonas amplias libres de obstáculos. No se debe usar en lugares húmedos o si el equipo está mojado, y la inteligencia artificial está adaptada a las muestras de una persona del equipo del proyecto, por lo que para ser usada por alguien mas se deberán muestrear los patrones de movimiento de esta misma.
En caso de que haya un error en la lectura de señales o haya un obstáculo en la trayectoria de la silla, se activará un sistema de emergencia. Su objetivo es prevenir accidentes y brindarle mayor seguridad al usuario. El sistema frena los motores y enciende un LED en la dirección del obstáculo, y enciende un buzzer, que enciende una señal sonora.
8.1.1. ¿Que es un EEG?

Un electroencefalógrafo es un dispositivo médico que se utiliza para registrar y medir la actividad eléctrica del cerebro. Su función principal es captar las señales eléctricas generadas por las neuronas cerebrales y transformarlas en gráficos de ondas cerebrales, que se pueden analizar para evaluar la función cerebral.

### 8.1.2. Componentes que tiene un EEG

Electrodos: Pequeños sensores que se colocan en el cuero cabelludo para captar los cambios de voltaje producidos por la actividad cerebral.

Amplificador: Como las señales eléctricas del cerebro son muy débiles, el electroencefalógrafo incluye amplificadores que aumentan la señal para que sea lo suficientemente fuerte como para ser registrada.

Conversor analógico-digital: Convierte las señales eléctricas captadas en un formato digital para su procesamiento por computadora.

Software de procesamiento: El dispositivo utiliza un software que transforma las señales en gráficos de ondas cerebrales que se presentan en tiempo real en una pantalla o se registran para análisis posterior.

Pantalla/Gráficos: El electroencefalógrafo muestra las señales eléctricas en forma de ondas, conocidas como ondas cerebrales (Delta, Theta, Alpha, Beta, Gamma), lo que permite a los médicos interpretar la actividad cerebral.

6

8.1.3. ¿Cómo se aplican los electrodos?

El sistema 10-20 es un método internacionalmente estandarizado para la colocación de electrodos en el cuero cabelludo durante un electroencefalograma (EEG). Este sistema asegura que los electrodos se coloquen de manera uniforme y precisa en relación con los puntos anatómicos del cráneo, permitiendo una medición consistente y reproducible de la actividad eléctrica cerebral.
El sistema 10-20 se utiliza para garantizar una colocación precisa y consistente de los electrodos en los estudios de EEG. Algunos de sus beneficios incluyen:

Estandarización global: Permite que los estudios de EEG sean comparables en diferentes laboratorios y entre diferentes pacientes.

Cobertura completa del cerebro: El sistema asegura que se cubran adecuadamente diferentes áreas del cerebro (frontal, parietal, occipital, temporal).

Detección de anomalías: Facilita la identificación de regiones del cerebro donde pueden estar ocurriendo fenómenos anormales, como descargas epilépticas, actividad lenta anormal o asimetrías en las ondas cerebrales.

El nombre "10-20"proviene de las distancias porcentuales entre los electrodos: Los electrodos se colocan en posiciones que están al 10 % o al 20 % de la distancia total entre puntos anatómicos clave del cráneo. Puntos anatómicos clave de referencia:

Nasion: El punto entre la frente y la nariz.

Inion: El punto más prominente en la parte posterior de la cabeza.

Puntos preauriculares: Justo por encima de los oídos, a cada lado de la cabeza.

Las posiciones de los electrodos se distribuyen sobre la cabeza tomando como referencia estos puntos para cubrir todo el cuero cabelludo de forma equidistante.
En la siguiente imágen se puede visualizar de mejor manera la posición de los electrodos:


Figura 3: Sistema 10-20

7

### 8.1.4. Pasos para aplicar el sistema 10-20

1. Medición del cráneo: Se mide la distancia desde el nasion al inion y desde un punto preauricular al otro. Luego, se calculan los puntos intermedios en un 10 o 20 de esas distancias para determinar las ubicaciones exactas de los electrodos.
2. Colocación de los electrodos: Se colocan electrodos en los puntos marcados, asegurando una cobertura uniforme de la cabeza. Esto puede hacerse usando una gorra de EEG con posiciones ya marcadas o mediante la medición manual.
3. Registro de la actividad: Una vez colocados los electrodos, se inicia el registro de la actividad cerebral. Los electrodos miden las diferencias de potencial eléctrico entre las regiones del cerebro cubiertas por los electrodos.

## 9. Desarrollo Técnico

En esta sección se desarrollarán y explicarán los distintos circuitos que conforman el dispositivo, así como los datos necesarios para comprender su funcionamiento y mantenimiento.

### 9.1. Funcionamiento del EEG

El sistema de control de nuestra silla de ruedas se basa en el reconocimiento de señales cerebrales, lo que requiere un dispositivo especializado para captarlas: el electroencefalograma (EEG). Hemos desarrollado un EEG en forma de una cofia equipada con electrodos, los cuales se colocan siguiendo el protocolo conocido como “Sistema 10-20”. Este sistema estándar de ubicación define puntos específicos en el cuero cabelludo donde se deben colocar los electrodos para obtener lecturas óptimas de la actividad cerebral.
Los electrodos actúan como sensores pasivos que detectan las ondas cerebrales producidas por la actividad eléctrica del cerebro. Estas ondas se manifiestan como pequeñas fluctuaciones en el voltaje, que son captadas por los electrodos cuando se colocan sobre la superficie del cuero cabelludo del usuario. Es importante destacar que estos electrodos no penetran en el cráneo ni interactúan directamente con las neuronas. En cambio, registran los potenciales eléctricos generados por la actividad cerebral subyacente que se propagan hasta la superficie del cuero cabelludo.
Debido a que las señales captadas por los electrodos son de muy baja amplitud, requieren ser amplificadas antes de su procesamiento. Este paso no solo amplifica la señal cerebral, sino también el ruido presente en el entorno o generado por el propio cuerpo. Para abordar este problema, se realiza un proceso de filtrado que elimina el ruido y permite aislar las frecuencias relevantes de las ondas cerebrales.
Las frecuencias de las ondas cerebrales detectadas son las siguientes:

Ondas alfa: 8-12 Hz

Ondas beta: 12-30 Hz

Ondas gamma: 30-100 Hz

Ondas delta: 0,5-4 Hz

Ondas theta: 4-8 Hz

Estas ondas cerebrales están asociadas con diferentes estados mentales y actividades cerebrales, por ejemplo, las ondas alfa se observan comúnmente en estados de relajación, mientras que las ondas beta se relacionan con un estado de alerta y concentración. Las ondas gamma, por otro lado, están vinculadas a procesos cognitivos de mayor complejidad, como la percepción y la conciencia. Las ondas delta y theta se asocian con fases profundas del sueño y la meditación.

8

### 9.2. Funcionamiento de los filtros HardWare

En un sistema de EEG, después de amplificar las señales captadas por los electrodos, se utilizan varios filtros para limpiar y mejorar la calidad de las señales antes de procesarlas o analizarlas. Estos filtros tienen un propósito importante: eliminar el ruido y enfocarse en las señales cerebrales relevantes.

### 9.2.1. Filtro Notch de 50 Hz

Propósito: Atenuación del ruido inducido por la red eléctrica de 50 Hz, común en muchos sistemas de distribución de energía.

Funcionamiento: El filtro Notch es un filtro de rechazo de banda estrecha, diseñado para eliminar una frecuencia específica (en este caso, 50 Hz) sin afectar significativamente las componentes de frecuencia cercanas o las señales EEG de interés. Las señales de EEG, que suelen estar en el rango de 0,5 a 40 Hz, pueden contaminarse por la interferencia de la red, por lo que este filtro resulta esencial para su eliminación sin alterar la información relevante.

### 9.2.2. Filtro pasa bajos de 100 Hz

Propósito: Reducción de las componentes de alta frecuencia que no son relevantes para el análisis EEG.

Funcionamiento: Este filtro pasa bajos permite el paso de frecuencias inferiores a 100 Hz, atenuando aquellas que exceden este umbral. Las señales cerebrales de interés generalmente se sitúan por debajo de los 40 Hz, aunque algunas pueden extenderse hasta 100 Hz. Este filtro elimina frecuencias más altas, que usualmente corresponden a interferencias electromagnéticas, ruido de dispositivos electrónicos o artefactos musculares (EMG).

### 9.2.3. Filtro pasa altos de 0,5 Hz

Propósito: Eliminación de las componentes de muy baja frecuencia, incluyendo artefactos de corriente continua (DC) y ruido de baja frecuencia no relacionado con la actividad cerebral.

Funcionamiento: El filtro pasa altos atenúa las señales con frecuencias por debajo de 0,5 Hz, permitiendo únicamente el paso de frecuencias superiores. La señal EEG relevante generalmente comienza en torno a los 0,5 Hz, mientras que frecuencias menores suelen estar asociadas a artefactos como el desplazamiento de los electrodos, fluctuaciones en la impedancia de los mismos, o interferencias lentas que no contienen información útil sobre la actividad cerebral.

### 9.3. Funcionamiento de los filtros digitales

Una vez que las ondas cerebrales son captadas y sometidas a un proceso inicial de filtrado, son transferidas a una Raspberry Pi 4. En este dispositivo se ejecuta un programa, desarrollado íntegramente por nuestro equipo, que continúa con el procesamiento y refinamiento de la señal. El motivo por el cual se aplica un filtrado adicional es que, luego de la etapa de filtrado inicial, la señal pasa por un segundo amplificador. Este amplificador, además de amplificar las señales cerebrales de interés, también amplifica el ruido residual presente en las mismas. Para contrarrestar este efecto, empleamos filtros digitales implementados por software, los cuales ofrecen una mayor precisión y control en la eliminación de interferencias no deseadas.
Dentro del programa, se han implementado los siguientes filtros:

Filtro Notch de 50 Hz: Este filtro está diseñado para eliminar las interferencias generadas por la red eléctrica, las cuales operan a una frecuencia de 50 Hz. Dado que estas interferencias pueden superponerse con la señal cerebral y distorsionar su interpretación, su eliminación es esencial para obtener un registro más fiel de la actividad cerebral.

9

Filtro Pasa-Bajo de 100 Hz: El objetivo de este filtro es retener las frecuencias cerebrales más relevantes, es decir, aquellas que se encuentran por debajo de los 100 Hz, mientras que elimina el ruido de alta frecuencia, que suele ser resultado de interferencias externas o artefactos no relacionados con la actividad cerebral. Este rango incluye frecuencias relacionadas con ritmos cerebrales importantes como las ondas alfa, beta, y gamma.

Filtro Pasa-Alto de 0,5 Hz: Este filtro se encarga de remover las señales de baja frecuencia que no aportan información útil sobre la actividad cerebral, como los artefactos causados por movimientos lentos o variaciones de corriente. Solo se permite el paso de las frecuencias EEG relevantes, garantizando que las señales reflejen con mayor precisión la actividad neural de interés.

Es importante señalar que el uso de estos filtros garantiza que la señal procesada esté lo más limpia posible de interferencias y artefactos, mejorando la precisión del sistema para detectar y procesar patrones cerebrales. La implementación de filtros mediante software, además, permite ajustar dinámicamente las configuraciones según las necesidades específicas del sistema y del entorno operativo, optimizando así el rendimiento de la silla de ruedas controlada por señales cerebrales.

### 9.4. Funcionamiento del Puente H

Un Puente H es un circuito utilizado para invertir el sentido de giro de un motor y para separar su etapa de potencia con la de control. Su nombre viene de la forma gráfica que tiene el circuito. Se construye con 4 interruptores, pueden ser mecánicos o transistores.
Nosotros optamos por diseñar un puente H de potencia, el cual es un tipo de circuito en el que la etapa de potencia, que incluye el motor, los transistores y está conectada a altas tensiones y corrientes, se encuentra separada de la etapa de control, la cual generalmente opera con voltajes más bajos. Esta separación se realiza para proteger la etapa de control de las altas tensiones, que podrían dañar o quemar sus circuitos.
El circuito que creamos utiliza dos señales PWM (PWM1 y PWM2) para controlar los transistores MOSFET en configuración de puente H, lo que permite invertir la polaridad del voltaje aplicado al motor, controlando así la dirección de rotación.
La velocidad del motor puede controlarse ajustando el ciclo de trabajo (duty cycle) de las señales PWM, que modulan la cantidad de energía entregada al motor.

### 9.4.1. Descripción de los Componentes

1. U1 y U2 (PC817 - Optoacopladores): Aíslan eléctricamente el circuito de control (de baja tensión) del circuito de potencia (de alta tensión). Esto protege al microcontrolador de posibles picos de voltaje y ruidos eléctricos provenientes del circuito de potencia. Cada optoacoplador tiene un LED interno que, al ser activado por una señal PWM, enciende un fototransistor interno, permitiendo que la señal de control pase al lado de potencia.
2. Q1 y Q3 (IRF4905 - MOSFET canal P): Actúan como interruptores en la parte superior del puente H. Controlan la alimentación positiva hacia el motor. Estos MOSFET se activan cuando la señal PWM1 o PWM2 está en bajo (0V) y se desactivan cuando está en alto (señal de 5V), debido a la naturaleza de los MOSFET de canal P.
3. Q2 y Q4 (IRF2805 - MOSFET canal N): Actúan como interruptores en la parte inferior del puente H. Conectan el motor a tierra cuando están activados. Estos MOSFET se activan cuando la señal PWM1 o PWM2 está en alto (5V) y se desactivan cuando está en bajo (0V).
4. R1 y R2 (Resistencias de 180 ohms): Limitan la corriente de entrada hacia los LEDs internos de los optoacopladores (U1 y U2) para protegerlos de daños.
5. R3 y R4 (Resistencias de 1k ohms): Están conectadas en serie con los MOSFET de canal P (Q1 y Q3). Limitan la corriente de la compuerta y aseguran un apagado rápido del MOSFET al detenerse la señal.

10

6. J1 y J2 (Conectores de entrada PWM): Reciben las señales PWM de control provenientes de un microcontrolador o una fuente de señal PWM.
7. J3 y J4 (Conectores de alimentación): Proveen la alimentación al circuito, uno con 24V para el motor y otro con 15V para los circuitos de control.
8. SW1 (Interruptor): utilizado para habilitar o deshabilitar el circuito completo, conectando o desconectando GND.

## 10. Circuitos usados

En este capítulo se incluirán imágenes de los esquemas de los circuitos, junto con su representación gráfica en formato virtual de los circuitos impresos, así como fotografías de los circuitos completos una vez finalizados.

### 10.1. Esquemático de los filtros


Figura 4: Esquemático de los filtros del EEG

### 10.2. Esquemático del sistema de control


Figura 5: Esquemáticos del sistema de control

11


### 10.3. Esquemático del sistema Offset

Figura 6: Esquemático del sistema de Offset

### 10.4. Esquemáticos de los Puentes H

Figura 7: Puente H (Un Motor)

12


### 10.5. Esquemático del sistema de emergencia

Figura 8: Esquemático del sistema de emegencia

(a) PCB Del sistema de emergencia | (b) Modelo 3D Del sistema de emergencia

13

## 11. Agradecimientos

Queremos expresar nuestro más profundo agradecimiento a los profesores que nos han brindado su invaluable apoyo en la realización de este proyecto:

Fabrizio Carlassara: Su asistencia fue crucial en la programación de la mayor parte del proyecto, así como en la creación de circuitos y esquemáticos, la búsqueda de materiales y el desarrollo de los filtros necesarios.

Sergio Medina: Nos brindó su experiencia en la presentación y comercialización del proyecto, además de colaborar en la programación, la búsqueda de materiales y la planificación de los puentes H.

Carlos Bianco: Su apoyo fue esencial en las pruebas y acondicionamiento de los motores, proporcionándonos herramientas y baterías para dichas pruebas, además de colaborar en la búsqueda de materiales.

Daniel Espósito: Nos proporcionó motores y materiales, además de enseñarnos a construir los puentes H para los motores y nos ayudó a solucionar problemas con las pistas de los circuitos para las altas corrientes.

Federico Solomiewicz: Colaboró principalmente en el desarrollo de los filtros, proporcionándonos herramientas para el proyecto y estando siempre disponible para resolver cualquier duda que surgiera.

Juan Carlos Ruiz: Su colaboración fue esencial en las pruebas de los motores para la silla de ruedas, además de ayudarnos principalmente en la creación de los puentes H para los motores y sus circuitos impresos.

14

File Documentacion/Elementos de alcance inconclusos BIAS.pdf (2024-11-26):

## Elementos de alcance inconclusos

En este documento se detallarán objetivos o funciones del proyecto que no se lograron llevar a cabo, junto a la razón de por qué decidimos descartarlas o no hacerlas.

1- Gabinete para el sistema de emergencias y los puentes H:
Empezando con los gabinetes para estos sistemas, queríamos mantener el proyecto estético y de paso proteger los circuitos ante cualquier residuo exterior, incluso realizamos los modelos 3D para la posterior impresión de los gabinetes para los sistemas. Debido a que en la escuela la impresora 3D estuvo con mal funcionamiento y el único compañero con impresora se quedó sin filamento a último momento, decidimos descartar esta idea.

2- Batería propia para el proyecto:
Este es un problema del que nos percatamos en el día de la exposición, ya que el grupo con el que compartíamos batería no nos prestó la batería en la exposición. Decidimos no comprar una propia ya que un profesor nos había prestado dos baterías de 12V (Necesitamos 24), pero no alcanzaba la corriente de estas. Es por esto que por todo el año usamos la batería de 24V de otro proyecto, además de que así abaratamos costos y podíamos usar ese dinero en otros componentes.

3- Asiento más cómodo para el proyecto:
El asiento verdaderamente no es práctico para una persona con problemas de movilidad, ya que siendo de madera y tan recto es completamente incómodo. El uso por un tiempo prolongado puede generar dolores de espalda. Por esto decidimos decir que se podría mejorar el asiento de la silla.

4- Jaula de faraday prolija:
La jaula de faraday que utilizamos para aislar del ruido eléctrico a los circuitos de filtrado está hecha principalmente por chapas recicladas, por lo que no queda tan prolijo como podría ser. Es un elemento que tiene margen de mejora.

5- Aislado de cables:
El aislado lo hicimos con termocontraible, por lo que realmente no es un aislado, sino que una forma de mantener los cables juntos y prolijos. En ciertas uniones no hay termocontraible por lo que es un elemento que también se puede mejorar.

6- Casco para colocación de electrodos
Al igual que los gabinetes, no pudimos realizar la impresión 3D de un casco para colocar los electródos, además de que requería mucha precisión ya que cada electrodo depende de la cabeza de uno, no era viable imprimir varios cascos.

7- Precisión de la IA
La IA aún puede entrenarse, ya que para poder mostrarla en las exposiciones tanto de las ONIET y del IMPA, tuvo menos entrenamiento del que debería. Este entrenamiento puede durar incluso meses, por lo que por temas de tiempo decidimos que puede ser mejorada.

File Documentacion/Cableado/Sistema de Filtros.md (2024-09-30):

Entrada:
[[EEG]] 
Salida:
[[Sistema de Offset]]

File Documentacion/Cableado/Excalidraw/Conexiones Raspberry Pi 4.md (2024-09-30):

---

excalidraw-plugin: parsed
tags: [excalidraw]

---
==⚠  Switch to EXCALIDRAW VIEW in the MORE OPTIONS menu of this document. ⚠== You can decompress Drawing data with the command palette: 'Decompress current Excalidraw file'. For more info check in plugin settings under 'Saving'

# Excalidraw Data
## Text Elements
+5V ^1OYYTSHh

Raspberry Pi 4 ^eVMHTeLq

%%
## Drawing
```compressed-json
N4KAkARALgngDgUwgLgAQQQDwMYEMA2AlgCYBOuA7hADTgQBuCpAzoQPYB2KqATLZMzYBXUtiRoIACyhQ4zZAHoFAc0JRJQgEYA6bGwC2CgF7N6hbEcK4OCtptbErHALRY8RMpWdx8Q1TdIEfARcZgRmBShcZQUebQBWbQBGGjoghH0EDihmbgBtcDBQMBLoeHF0QOwojmVg1JLIRhZ2LjQAFgB2flLm1k4AOU4xbgAOeKSATniANlGeAGYeyEIO

YixuCFwABgbSwmYAEXSoBGJuADMCMOWIEk2AeQB1DlGAUQAlBYA1ZSSARwAQm8ACoALVInVwF2cRj2kAuhHw+AAyrB6hJBB54RBmFBSGwANYIJ4kdTcPiFAT4okINEwDHoLH3W4EvySDjhXJoJK3NhwXDYNQwbhJbbbW7WOoVCVUiCYbjOJIzSmNCAitBKibadpJdrbFXxW54gnEgDCbHwbFImwAxEkEA6HTjNILCco2WsLVabRJ8dZmALAtkcRQ

yZJuAskqNbpIEIRlNIKTwY3KwmdRaNOp1xQttgslnKPcI4ABJYjc1B5AC6twu5Ey5e4HCEyNZwjWnOYleKatgiEjVIAvrdNB3iG9gplspWCo0ilT9ucJMoQQBZJLYABWKOYPGc/wQCG+mgoAGlAQApOAABXhpX7FS2pAJVEXQ6ptblQjgxFwp2XVAkk6Hhs2jeJJhmTp9VuIgOEJZtW3wWC2GwYlAKufAwkKEdCl7SBH02XAXzYKhbj6VpI1VXom

H6Dghg4EY0EmUYVRA2ZujlVZ1gVCRcBSW4DmOYIAMua4EEEwCIFXDdt13fdD2PU8L2vO86yRVF0SfZlzmNGliVJYhyTQajqVNOktM2HScTZRMu0rXk5X5QVhVFcVJVqRlZTVXjUGcFNUzVDU/LFGYdT1A0eCNNN9IQb1rTtJ1HSQUc3WLIQvUtBK/XIDhA2IrIoFDcNRWjWN40TIqeWNI9AKSeJ2lYnhdVGQs1XSssK3yL81XrXBG0Als2zlT1iH

s7h8II8oKWHUdx0nDJCtnHrSh/P9RJ5ECwPGSDOgWSZYNWBC0CG5C5StNCMzQTCbhi4ioEBbjVmURDhrVLJiEetZnomxcMCnQqmwkZ5Xk+H4/iBUEIShGE4WWBFUKESttm0GYpiSKN4lGLouhmPNOPnaTcDgMZ4YgRFMDOG82FWKrUFO2bztCKALX0fQ1AA6nades61Txe6AEESIoONcEGpDbg+oXX1FqTiNfHE4Bpmd8kXOd528jXFxWkp1caJI
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

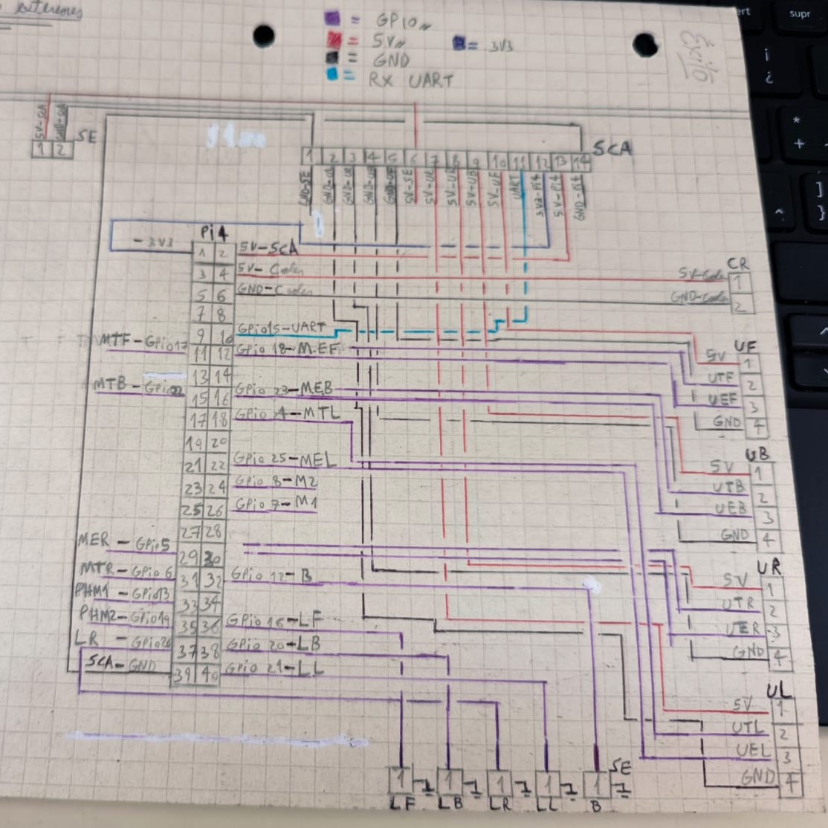
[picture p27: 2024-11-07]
circuitos/Cableado/Interconexiones/Diseño de interconexiones.jpeg

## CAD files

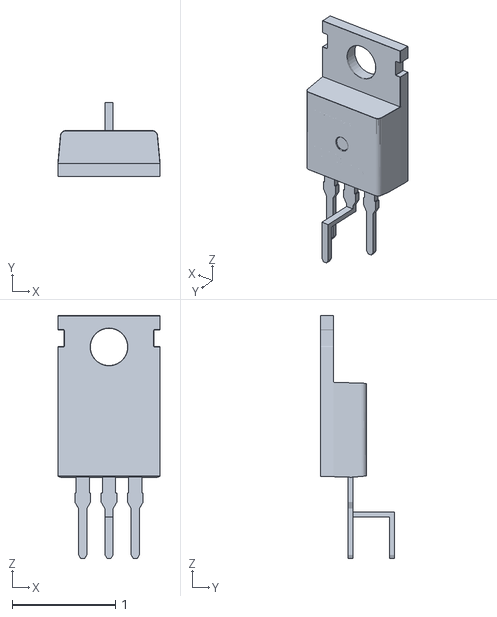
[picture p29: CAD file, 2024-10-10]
circuitos/Puente H/Revisiones Viejas/puente h doble rev13/puente h doble rev8.1.7/puente h doble rev8.1.5/User Library-TO220-A PCB ga2.stl
0.99 x 0.717 x 2.35

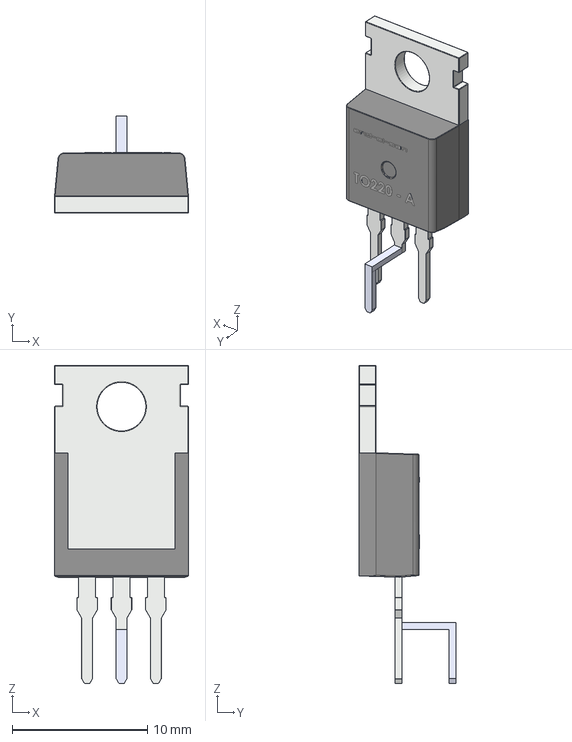
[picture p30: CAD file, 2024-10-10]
circuitos/Puente H/Revisiones Viejas/puente h doble rev13/puente h doble rev8.1.7/User Library-TO220-A PCB ga1.step
9.90 x 7.17 x 23.5 mm

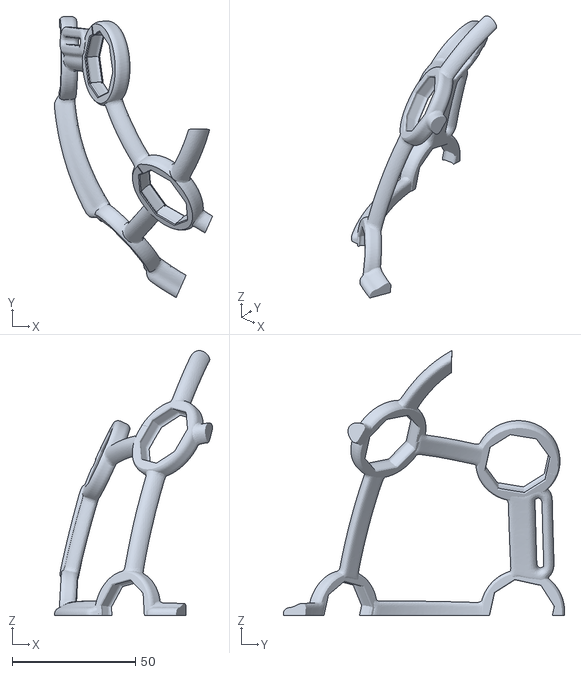
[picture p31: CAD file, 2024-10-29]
Documentacion/Modelado 3D/EEG/STL/left-front.stl
64.3 x 114.3 x 107.7

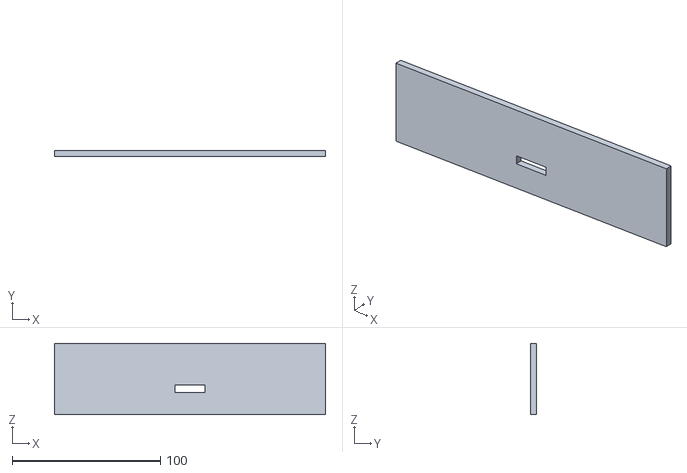
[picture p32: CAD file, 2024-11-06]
Documentacion/Modelado 3D/Gabinete Puente H/STLs/CostadoLargoPinesGabinete.stl
183.0 x 4.00 x 48.0

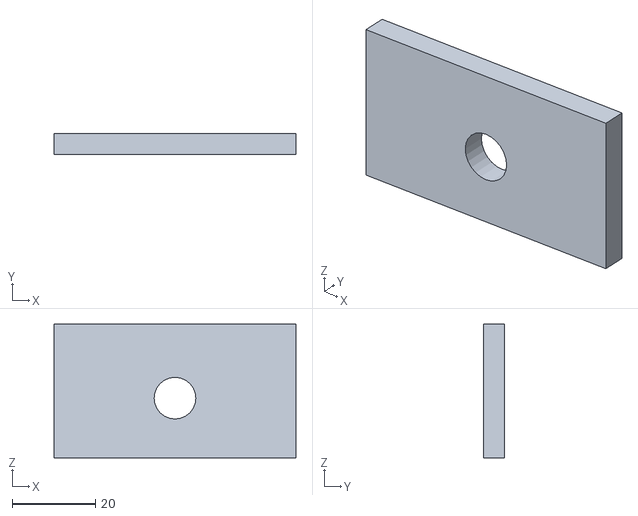
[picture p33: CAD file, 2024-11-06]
Documentacion/Modelado 3D/Sistema de emergencias/ParteTrasera.stl
58.0 x 5.00 x 32.0

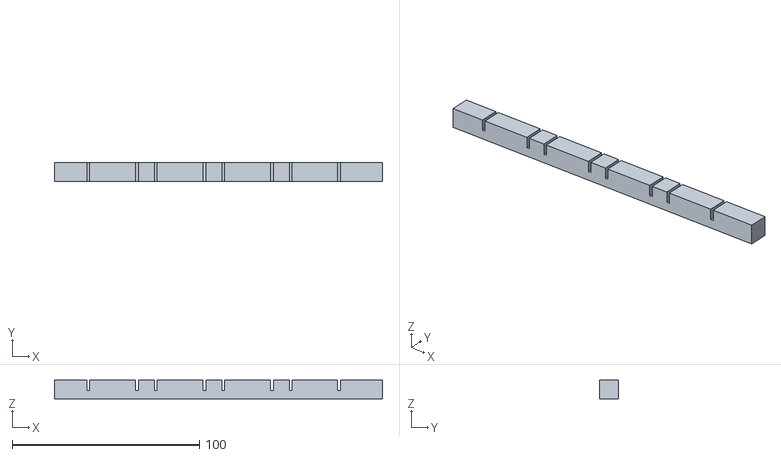
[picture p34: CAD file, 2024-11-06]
Documentacion/Modelado 3D/Varilla para Disipadores/SoporteGabinete.stl
175.0 x 10.0 x 10.00

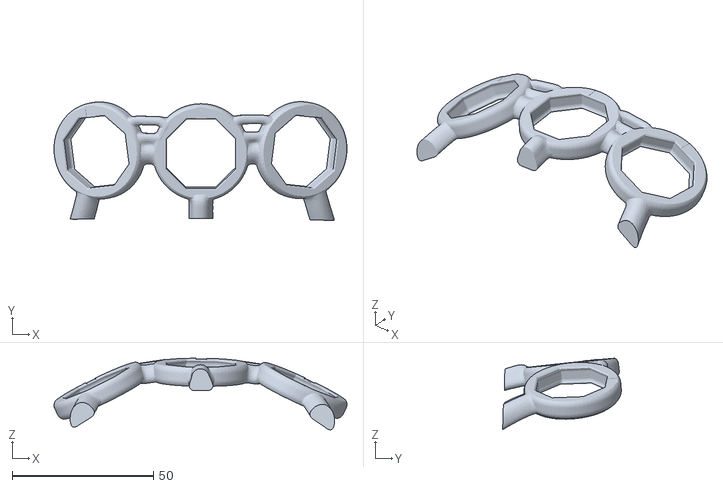
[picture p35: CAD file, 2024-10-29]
Modelado 3D/EEG/STL/top-front.stl
103.7 x 42.0 x 25.4

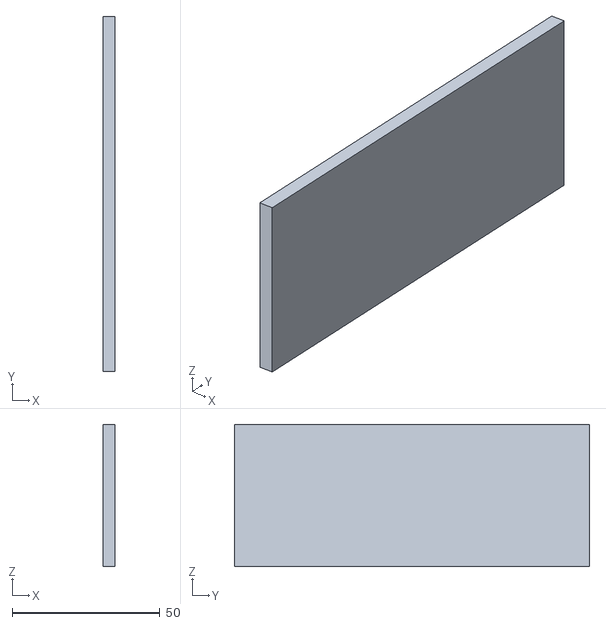
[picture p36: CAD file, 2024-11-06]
Modelado 3D/Gabinete Puente H/STLs/CostadoCortoGabinete.stl
4.00 x 120.0 x 48.0

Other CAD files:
Documentacion/Modelado 3D/Sistema de emergencias/SistemaEmergenciasFull.dwg
Modelado 3D/Sistema de emergencias/SistemaEmergenciasFull.dwg
Documentacion/Modelado 3D/EEG/STL/center-front.stl
Documentacion/Modelado 3D/EEG/STL/right-front.stl
Documentacion/Modelado 3D/EEG/STL/segmented-front.stl
Documentacion/Modelado 3D/Gabinete Puente H/CostadoCortoGabinete.dwg
Documentacion/Modelado 3D/Gabinete Puente H/CostadoLargoBornerasGabinete.dwg
Documentacion/Modelado 3D/Gabinete Puente H/CostadoLargoPinesGabinete.dwg
Documentacion/Modelado 3D/Gabinete Puente H/ParteArribaGabinete.dwg
Documentacion/Modelado 3D/Gabinete Puente H/ParteBajaGabinete.dwg
Documentacion/Modelado 3D/Gabinete Puente H/STLs/CostadoLargoBornerasGabinete.stl
Documentacion/Modelado 3D/Gabinete Puente H/STLs/ParteArribaGabinete.stl
Documentacion/Modelado 3D/Gabinete Puente H/STLs/ParteBajaGabinete.stl
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

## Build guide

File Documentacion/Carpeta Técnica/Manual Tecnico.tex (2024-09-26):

\documentclass{article} 
\usepackage[utf8]{inputenc} 
\usepackage[spanish]{babel}
\usepackage{graphicx} 
\usepackage{subcaption}
\usepackage{hyperref}
\usepackage{listings}
\usepackage{xcolor}
\usepackage{float}

\definecolor{codegreen}{rgb}{0,0.6,0}
\definecolor{codegray}{rgb}{0.5,0.5,0.5}
\definecolor{codepurple}{rgb}{0.58,0,0.82}
\definecolor{backcolour}{rgb}{0.95,0.95,0.92}

\lstdefinestyle{mystyle}{
    backgroundcolor=\color{backcolour},
    commentstyle=\color{codegreen},
    keywordstyle=\color{blue},
    numberstyle=\tiny\color{codegray},
    stringstyle=\color{codepurple},
    basicstyle=\ttfamily\footnotesize,
    breakatwhitespace=false,
    breaklines=true,
    captionpos=b,
    keepspaces=true,
    numbers=left,
    numbersep=5pt,
    showspaces=false,
    showstringspaces=false,
    showtabs=false,
    tabsize=2
}

\lstdefinelanguage{CSS}{
  keywords={color,background-image:,margin,padding,font,weight,display,position,top,left,right,bottom,list,style,border,size,white,space,min,width, transition:, transform:, transition-property, transition-duration, transition-timing-function},	
  sensitive=true,
  morecomment=[l]{//},
  morecomment=[s]{/*}{*/},
  morestring=[b]',
  morestring=[b]",
  alsoletter={:},
  alsodigit={-}
}
\lstset{style=mystyle}
\date{} 

\begin{document} 

\begin{center}
    \\ 
\end{center}
    
\title{BIAS} 

\vspace{1cm} 

\textbf{Integrantes del Proyecto:} 

\begin{itemize}
    \item Adell, Nicolas Fabian
    \item De Blasi, Luca
    \item Diaz Melion, Danilo Sebastian
    \item Gil Soria, Ian Lucas
    \item Montenegro, Luciano Nahuel
    \item Sojka, Santiago Alejandro
\end{itemize}

\tableofcontents 

\newpage 

\section{Introducción}

BIAS es un módulo aplicable a una silla de ruedas que permite el control mental, permitiendo a los usuarios dirigirla mediante el sus pensamientos, eliminando la necesidad de controles físicos tradicionales y optimizando la experiencia de movilidad. Este proyecto representa un avance significativo en el campo de la movilidad asistida, con el objetivo de mejorar la independencia y la calidad de vida de las personas con movilidad reducida.

Este sistema se basa en la avanzada tecnología de interfaz cerebro-computadora (BCI), la cual captura las señales neuronales del usuario y las traduce en comandos precisos para maniobrar la silla de ruedas sin esfuerzo. Además, el diseño modular y adaptable del sistema permite su integración en diversos modelos de sillas de ruedas y su personalización según las necesidades específicas de cada usuario. 

La seguridad es una prioridad fundamental en este desarrollo, por lo que el módulo incorpora múltiples capas de redundancia y verificación de señales, asegurando que la silla de ruedas responda de manera precisa y confiable a las intenciones del usuario. 

Aspiramos a revolucionar la forma en que las personas con movilidad reducida interactúan con su entorno, brindándoles una herramienta que amplía su capacidad para controlar su vida de manera más segura e independiente.

\subsection{Resumen del proyecto}
Este proyecto se centra en el desarrollo de una silla de ruedas controlada mediante señales cerebrales. El sistema se compone principalmente de los siguientes componentes: la silla de ruedas, un dispositivo EEG (electroencefalograma) y dos motores que permiten al usuario moverse en la dirección deseada.

El funcionamiento del sistema es el siguiente: el usuario se sienta en la silla y se coloca el EEG en la cabeza. A continuación, el usuario piensa en la dirección en la que desea moverse, y los motores responden en consecuencia.

El EEG tiene la función de leer las señales cerebrales del usuario. Estas señales se clasifican en las categorías de alpha, beta, gamma, delta y theta, y luego se someten a un proceso de filtrado para eliminar cualquier ruido. Posteriormente, las señales filtradas son analizadas por una Inteligencia Artificial (IA) desarrollada por nuestro equipo, la cual identifica patrones para determinar si el usuario desea moverse o detenerse.

Además, la silla está equipada con un sistema de emergencia que se activa en caso de lecturas erróneas o la detección de obstáculos. Este sistema de emergencia está compuesto por sensores infrarrojos y ultrasónicos que detectan la presencia de obstáculos frente a la silla.

\subsection{Motivación}
Como estudiantes de séptimo año, buscamos desarrollar un proyecto con el fin de cumplir con el requerimiento horario de practicas profesionalizantes. Nuestra intención inicial fue encontrar el proyecto ideal en cuestiones de impacto social, enfocándonos en la mejora de la calidad de vida de aquellas personas con discapacidades. Bajo este marco, y tras una extensa investigación, proponemos crear un módulo aplicable a una silla de ruedas controlado mediante la actividad cerebral del usuario, utilizando tecnología de interfaces cerebro-computadora (BCI), para brindarles mayor autonomía, independencia y participación social.   Creemos que este proyecto tiene el potencial de transformar la vida de las personas con movilidad motora reducida debido a enfermedades como ELA, esclerosis múltiple o cuadriplejia, permitiéndoles controlar su propio movimiento y mejorar significativamente su calidad de vida.
\subsection{Objetivos}
El objetivo de este proyecto es desarrollar una silla de ruedas motorizada que pueda ser controlada por la actividad cerebral del usuario. Esto beneficiaría a las personas con discapacidades motoras severas para lograr independencia y movilidad, mejorando su calidad de vida y participación en la sociedad. De esta manera, estas personas las cuales no pueden caminar o tienen movilidad reducida, pueden gozar de la utilización de una silla de ruedas controlada por señales cerebrales sin la utilización de ambas manos y meramente por sus pensamientos, dándole libertad y autonomía al usuario.

\section{¿Quiénes somos?}
Somos el grupo BIAS (Brain Intelligence Artificial System), conformado por seis estudiantes de la especialidad de Aviónica del séptimo año, segunda división, comisión " C ", de la Escuela Técnica N° 7 IMPA "Taller Regional Quilmes". Nuestro equipo se encuentra comprometido en el desarrollo de un módulo adaptable para sillas de ruedas, para así poder brindarles mas independencia y movilidad.
\subsection{Contactos}

En este apartado se detallarán los contactos a los integrantes del proyecto, adjuntando enlaces a sus redes:

\subsubsection{Adell Nicolás}

    \href{https://instagram.com/nicolas.adell}{Instagram}

    \href{http://www.linkedin.com/in/nicolas-adell-354508297}{LinkedIn}

    \href{mailto:nicolas.fabian2005@gmail.com}{Gmail}

\subsubsection{De Blasi Luca}

    \href{https://instagram.com/luca.deblasii}{Instagram}

    \href{https://www.linkedin.com/in/luca-de-blasi-31164b304}{LinkedIn}

    \href{mailto:luqac2006@gmail.com}{Gmail}

\subsubsection{Diaz Melión Danilo}

    \href{https://instagram.com/_danilodiaz}{Instagram}

    \href{https://www.linkedin.com/in/danilodiazmelion/}{LinkedIn}

    \href{mailto:danilodiaz934@gmail.com}{Gmail}

\subsubsection{Gil Soria Ian}

    \href{https://instagram.com/ian_gilsooor}{Instagram}

    \href{https://www.linkedin.com/in/ian-lucas-gil-soria-a8090b2a8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}{LinkedIn}

    \href{mailto:ianlucasgilsoria@gmail.com}{Gmail}

\subsubsection{Montenegro Luciano}

    \href{https://instagram.com/luchito_.montenegro}{Instagram}

    \href{https://www.linkedin.com/in/luciano-montenegro-3215aa304}{LinkedIn}

    \href{mailto:lucianomontenegro1021@gmail.com}{Gmail}

\subsubsection{Sojka Santiago}

    \href{https://instagram.com/sojkaa.sant}{Instagram}

    \href{https://www.linkedin.com/in/santiago-sojka-817198271/}{LinkedIn}

    \href{mailto:santiagosojka@gmail.com}{Gmail}

\section{Desarrollo del Proyecto}
En este capítulo se expondrá en detalle la metodología empleada para avanzar en el desarrollo del proyecto, incluyendo las fuentes de inspiración y los proyectos similares que se tomaron como referencia para el diseño de nuestros circuitos y la programación de los sistemas. Además, se incluirán imágenes ilustrativas de estos proyectos de referencia, con el fin de ofrecer una comprensión visual más completa. Al finalizar el capítulo, se presentarán y explicarán los resultados obtenidos, evaluando su eficacia en relación con los objetivos planteados.

\subsection{Metodología}
La metodología aplicada en este proyecto se basa en la organización del equipo en dos grupos especializados. El primer grupo se encarga del desarrollo de los programas, siendo ejemplos de esto los filtros virtuales, programas de recepción y procesado, mientras que el segundo se dedica a la implementación de los motores, sistemas de emergencia y filtros. Esta división del trabajo permite una utilización más eficiente del tiempo, al abordar simultáneamente diversas áreas del proyecto, lo que resulta en un avance más significativo en periodos de tiempo más reducidos.

\subsection{Historia del Arte}
En este capitulo se repasa todos los conceptos previamente vistos mediante los cuales pudimos empezar a conceptualizar la idea del proyecto.

\subsubsection{Neuralink}
Uno de los casos que nos permitió aproximarnos a la conceptualización del proyecto fue el chip cerebral estilo implante de Neuralink, denominado Telepathy. Este dispositivo, desarrollado por la compañía de Elon Musk, tiene como objetivo facilitar la vida de las personas mediante la optimización de herramientas y su adaptación al cuerpo humano a través del implante. El chip crea una conexión entre el ser humano y dispositivos electrónicos, permitiendo, por ejemplo, controlar una puerta con traba eléctrica, desbloquear un teléfono móvil, e incluso monitorear el estado de ánimo de las personas.

Este ejemplo nos ofreció una perspectiva sobre la viabilidad de desarrollar un dispositivo, que, aunque no tan complejo, pudiera ser controlado por el propio cuerpo humano. A partir de esta premisa, iniciamos una investigación para explorar las posibilidades y opciones disponibles basadas en esta idea.

\subsubsection{Ryan Lopez EEG}
Si bien nuestro motivo y objetivo principal era crear un dispositivo original e innovador, también nos propusimos investigar proyectos con cierta similitud. En este proceso, encontramos el repositorio de un estudiante que desarrolló un sistema capaz de detectar señales alfa y, en función de las reacciones o pensamientos del usuario, permitir el control a través de un test de concentración. Este test consistía en que el usuario debía mantener un estado de concentración mientras estudiaba un documento para un examen, en lo que se podría considerar un simulacro.

El sistema desarrollado por Ryanlopezz activaba una alarma si los niveles de concentración del usuario comenzaban a disminuir, basándose en un espectro de señales alfa transmitidas por un conjunto de electrodos EEG dorados conectados a la cabeza del estudiante. Además, el sistema realizaba otras dos pruebas: una de ellas consistía en escribir en código Morse mediante pensamientos, enviando "pulsos de concentración", y la otra permitía controlar el movimiento de un personaje en el famoso videojuego "Flappy Bird", ajustando el impulso para subir o bajar.

En el siguiente link se adjunta la página de GitHub de Ryan Lopez en donde se puede observar más a detalle los programas y archivos de su EEG.

\begin{center}
    \href{https://github.com/ryanlopezzzz/EEG}{Ryan Lopez GitHub}
\end{center}

Gracias al mismo proyecto realizado por este usuario, pudimos desarrollar nuestro propio circuito para el sistema de filtrado, ya que íbamos a requerir otras especificaciones con diferentes funciones, tales como la entrada de señal: ya que esta debía ser mayor a la designada, al nosotros trabajar no solo con el espectro radioelectrico de las señales Alpha, sino con las principales señales que el cerebro produce al momento de realizar un pensamiento especifico; Por otro lado nosotros íbamos a requerir no solo un sistema de filtros EEG sino 4 placas del mismo circuito, debido a la posibilidad de maniobrar controlando los 3 ejes de los motores de la silla de ruedas

\begin{center}
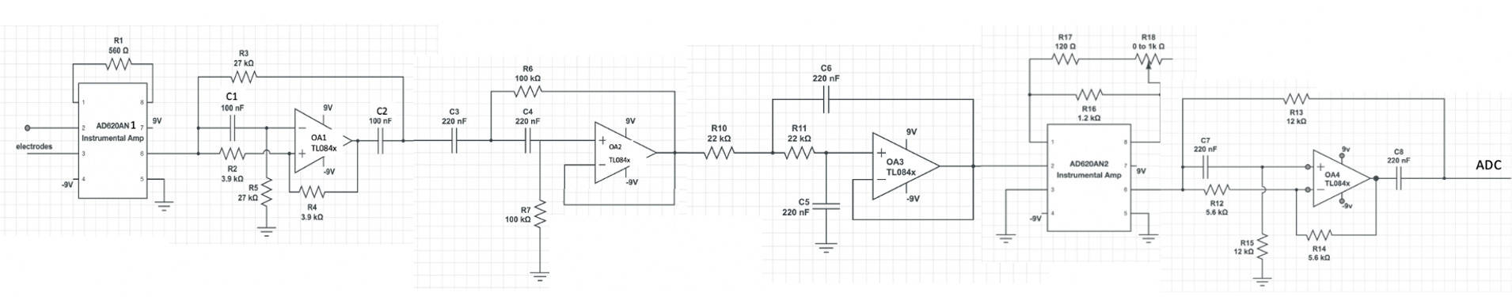
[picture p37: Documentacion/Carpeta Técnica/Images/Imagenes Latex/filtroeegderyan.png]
    \\
    
Por otro lado nos dio una primera vista de la localización de los botones EEG como irían colocados en la cabeza

\end{center}

\begin{center}
    \\

\end{center}

Así mismo para el estudio del aérea de medicina y saber como el cerebro humano se encarga de transmitir ciertas señales eléctricas gracias a la actividad cerebral  tuvimos en cuenta los actuales dispositivos de eneflografos, como se componen y actúan gracias ala actividad cerebral, bajo un especto radioelectrico determinado adjunto a la clasificación de las ondas transmitidas por el cerebro humano

\subsubsection{OpenBCI}

En nuestra búsqueda de conexiones para un microcontrolador y formas de desarrollar nuestro propio proyecto, descubrimos un sitio web llamado OpenBCI, una compañía especializada en la creación de dispositivos que integran tecnología con la interfaz del cuerpo humano. Esta empresa ha desarrollado un encefalógrafo casero, proporcionando dimensiones y parámetros estructurales que nos permitieron diseñar nuestra propia vincha/casco. Este dispositivo incorpora electrodos EEG, adaptados a la cabeza del usuario, como parte fundamental de nuestro proyecto "BIAS".

\begin{center}
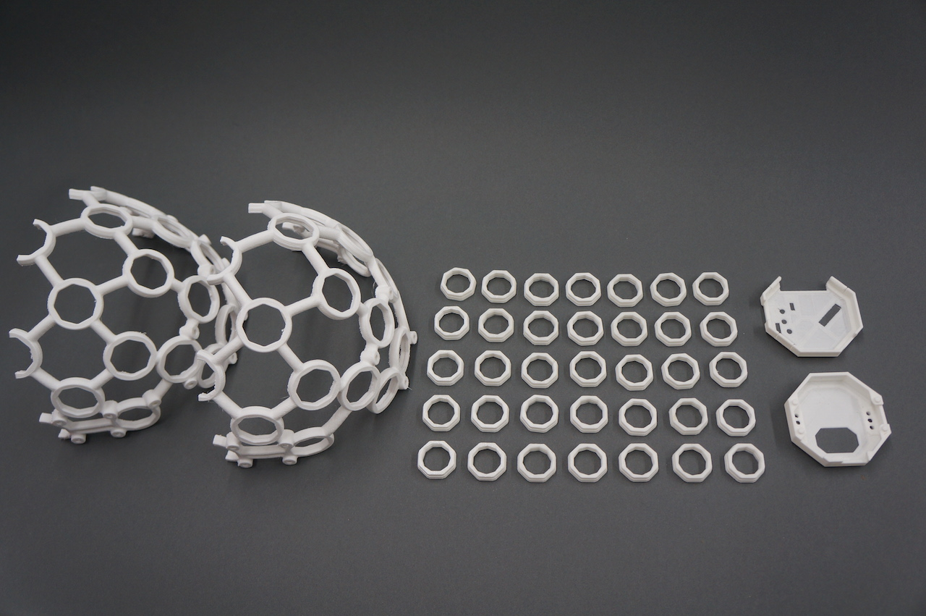
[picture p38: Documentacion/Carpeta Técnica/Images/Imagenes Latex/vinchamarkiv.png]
    \\
\end{center}

Además, al ser una compañía especializada en la creación de módulos de microcontroladores, nos proporcionaron orientación en cuanto a cómo realizar las conexiones entre la Raspberry Pi 4 que utilizamos y el sistema de filtrado EEG.

En los siguientes textos se adjuntan enlaces para ver la página oficial de OpenBCI y documentación de referencia correspondiente.

\begin{center}
    \href{https://openbci.com/}{Página oficial de OpenBCI}

    \href{https://docs.openbci.com/}{Documentación}

\end{center}

\begin{figure}[h!]
\centering

\begin{subfigure}[b]{0.45\linewidth}
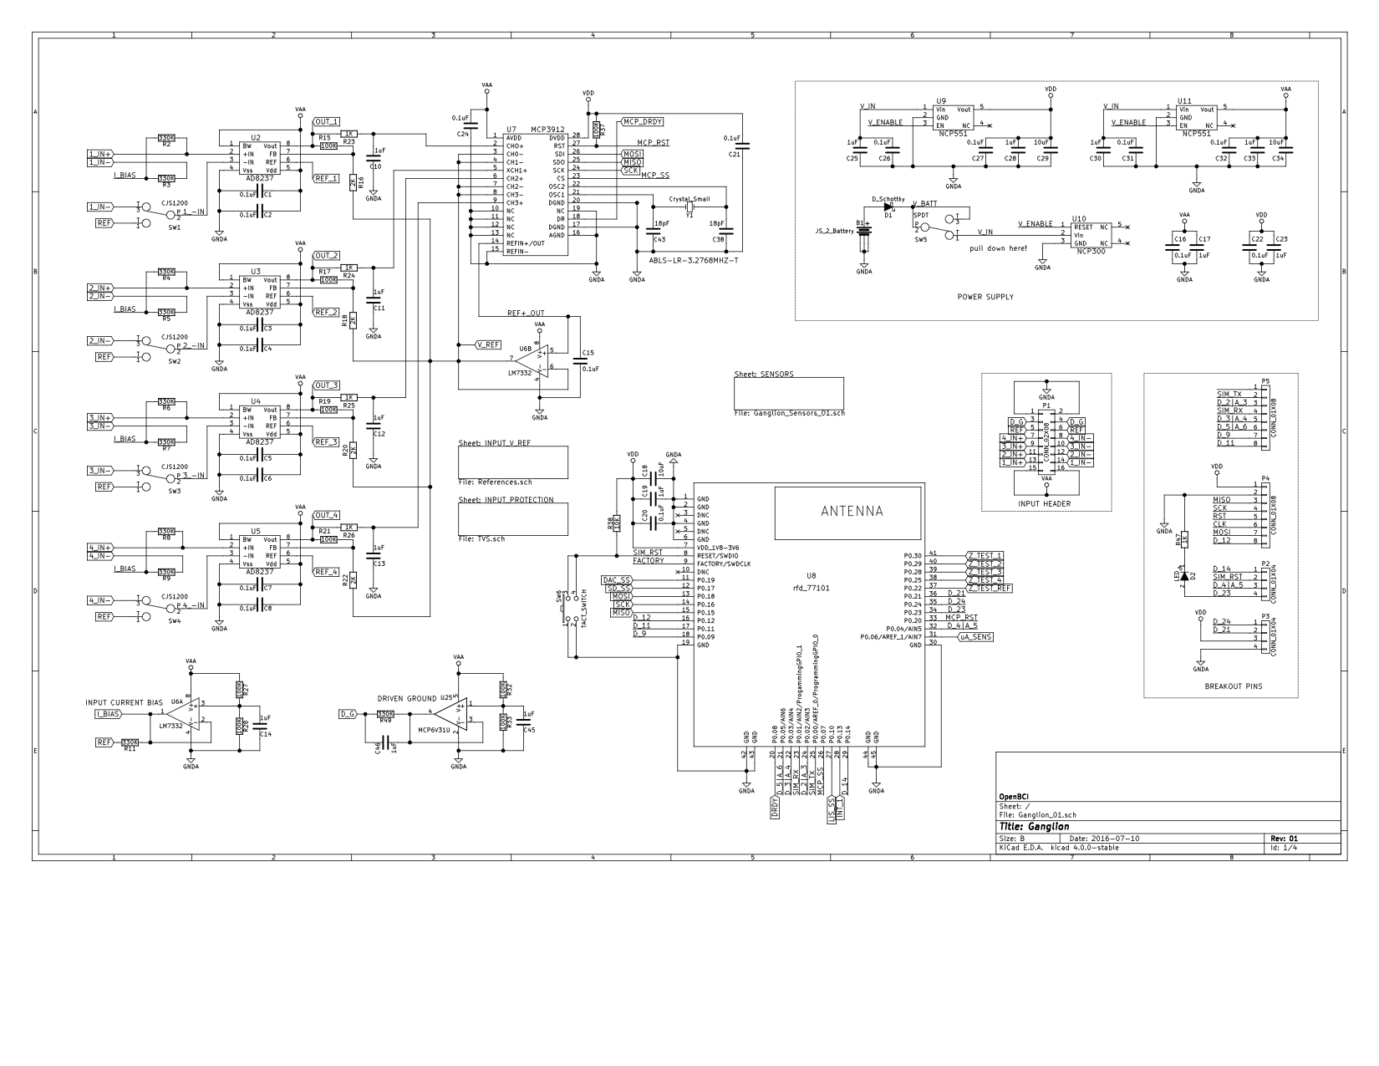
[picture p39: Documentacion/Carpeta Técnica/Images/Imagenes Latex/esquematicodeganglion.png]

\caption{Diseño Esquemático}
\label{fig:westminster_lateral}
\end{subfigure}

\begin{subfigure}[b]{0.45\linewidth}
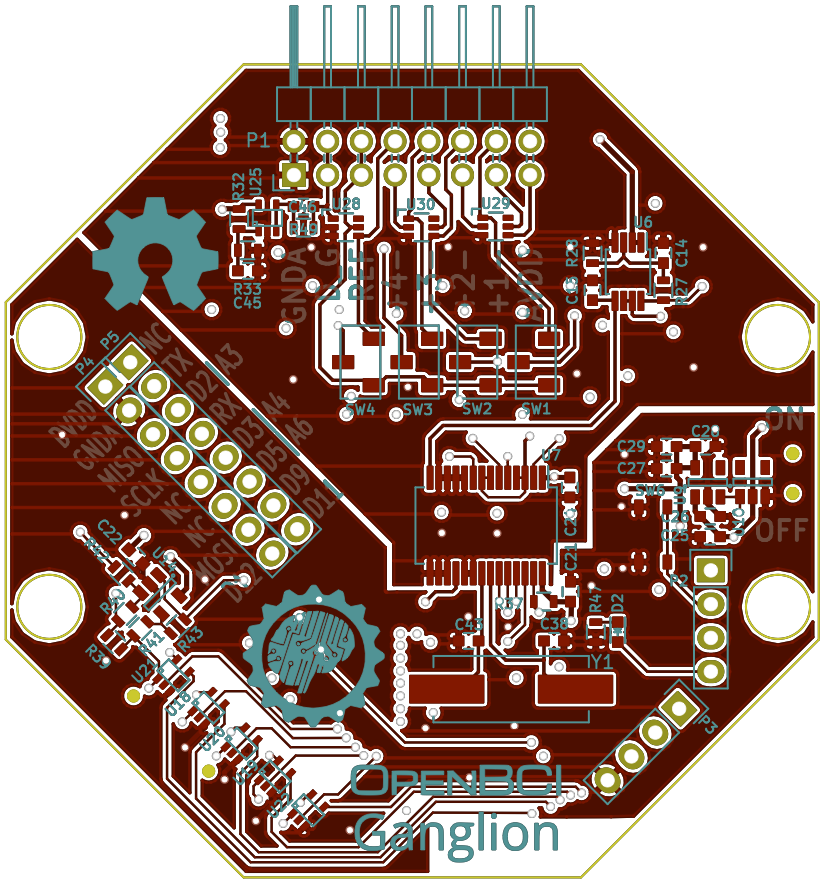
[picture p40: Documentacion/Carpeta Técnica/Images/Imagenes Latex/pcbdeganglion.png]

\caption{DIseño PCB}
\label{fig:westminster_aerea}

\end{subfigure}
\caption{Diseño de microcontrolador de Open BCI}
\label{fig:westminster}
\end{figure}

\begin{center}
    \\

    \\
\end {center}

\section{Desarrollo Teórico}
En este capítulo se describirán y desarrollarán todos los aspectos teóricos relacionados, justificando la elección de los componentes utilizados. Se abordarán teorías como la Jaula de Faraday y el sistema 10-20, además de ofrecer una explicación detallada sobre los tipos de señales empleadas, entre otros temas relevantes.

\subsection{Distinción de alimentaciones}

\subsection{Sistema 10-20}

\subsection{Comunicación UART}

\subsection{Gráfico de Fourier}
que es
por que la necesitamos
como lo aplicamos
Explicar ondas cerebrales

\subsection{Filtros digitales}

\subsection{Cantidad de canales}

\subsection{Uso del gel conductor}
que es
por que la necesitamos
como lo aplicamos

\subsection{Jaula de Faraday}
Una jaula de Faraday es, esencialmente, una estructura metálica diseñada para proteger su interior de los campos eléctricos estáticos. Su nombre proviene del físico Michael Faraday, quien construyó la primera de estas estructuras en 1836. Las jaulas de Faraday se utilizan para proteger su contenido de descargas eléctricas y del ruido electromagnético, debido a que, en su interior, el campo eléctrico es nulo. Su principio de funcionamiento se basa en las propiedades de un conductor en equilibrio electrostático, lo que impide que cualquier carga eléctrica atraviese la estructura. Por esta razón, se emplean para proteger dispositivos sensibles a las cargas eléctricas. Este fenómeno es conocido como apantallamiento eléctrico.

\subsubsection{¿Por qué utilizamos una Jaula de Faraday?}
Dado que trabajamos con señales altamente susceptibles al ruido debido a su frecuencia y voltaje, como es el caso de las señales captadas por el EEG, es fundamental mantenerlas lo más aisladas posible de interferencias externas. Además, contamos con una fuente importante de ruido electromagnético: el motor. Por esta razón, es esencial posicionar los componentes lo más alejados posible entre sí y utilizar una Jaula de Faraday en la sección destinada a la recepción y procesamiento de las señales.

La implementación de este elemento se realiza mediante una caja metálica que será ubicada en la parte superior trasera de la silla de ruedas, es decir, en la zona de apoyo de la espalda, para mantenerla lo más distante posible de los motores.

\subsection{Utilización de offsets}

\subsection{Sistema de emergencia}

\subsection{Tipos de alimentaciones}

\subsection{Sistema de control}

\subsection{Puentes H}
Un Puente H es un circuito utilizado para invertir el sentido de giro de un motor y para separar su etapa de potencia con la de control. Su nombre viene de la forma gráfica que tiene el circuito. Se construye con 4 interruptores, pueden ser mecánicos o transistores. En la siguiente imágen se puede ver la forma de un puente H.

\begin{figure}[H]
    \centering
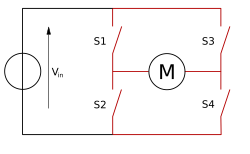
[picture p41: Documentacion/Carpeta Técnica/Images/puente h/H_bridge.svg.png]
    
    \caption{Puente H Genérico por medio de llaves mecánicas}
\end{figure}

En este ejemplo, cuando la llave S1 y S4 se cierran, correrá corriente por esta rama, haciendo que el motor funcione y tenga un sentido de giro. Cuando la llave S2 y S3 se cierran, correrá corriente por esta rama también, pero con sentido de giro invertido. En este circuito, S1 y S2 nunca pueden estar cerradas al mismo tiempo, porque esto generaría un corto circuito, lo mismo con las llaves S3 y S4.

\begin{figure}[H]
    \centering
    
    \caption{Puente H Operando}
\end{figure}

Un puente H de potencia es un tipo de circuito en el que la etapa de potencia, que incluye el motor, los transistores y está conectada a altas tensiones y corrientes, se encuentra separada de la etapa de control, la cual generalmente opera con voltajes más bajos. Esta separación se realiza para proteger la etapa de control de las altas tensiones, que podrían dañar o quemar sus circuitos. Podemos utilizar nuestro puente H como ejemplo para ilustrar este concepto:

 \begin{figure}[H]
     \centering
     
     \caption{Nuestro Puente H de potencia}
     \label{fig:enter-label}
 \end{figure}

En nuestro puente H, hemos separado las ramas del motor de las de control, ya que el motor opera con 24V DC y tiene una corriente eficaz de 5A. Para controlar el motor de manera eficiente, hemos optado por un diseño que incluye cuatro transistores MOSFET de potencia, los cuales pueden soportar picos de hasta 74A y 82A, garantizando que puedan manejar la corriente del motor de manera continua. Además, los transistores son controlados mediante señales PWM, las cuales atraviesan un optoacoplador para minimizar el riesgo de que la corriente del motor regrese a la placa de control y cause daños. De ésta manera, podemos controlar el giro del motor de manera segura y regulada.

\subsection{Sistema de recepción de señales}

\subsection{Control por PWM}
La modulación por ancho de pulso (PWM, por sus siglas en inglés Pulse Width Modulation) es una técnica empleada para regular la cantidad de energía suministrada a una carga, como un motor o un LED, mediante la variación del ciclo de trabajo de una señal pulsante. En lugar de modificar el voltaje de forma continua, PWM ajusta el tiempo durante el cual la señal permanece en estado alto (encendida) y bajo (apagada) dentro de un período fijo. Esto depende de los siguientes parámetros:

Frecuencia: Se refiere a la cantidad de ciclos de encendido y apagado que ocurren en un segundo, y se mide en Hertz (Hz).

Ciclo de trabajo: Es el porcentaje de tiempo que la señal se mantiene en estado alto durante un ciclo. Por ejemplo:

Un ciclo de trabajo del 0\% implica que la señal está siempre apagada.

Un ciclo de trabajo del 50\% significa que la señal está encendida la mitad del tiempo y apagada la otra mitad.

Un ciclo de trabajo del 100\% indica que la señal permanece siempre encendida.

En nuestro proyecto, aplicamos la técnica de PWM en el control de los motores. Dado que utilizamos dos motores, si estos operaran a su máxima potencia, la silla de ruedas se desplazaría a una velocidad excesiva. Por esta razón, empleamos un ciclo de trabajo del 25\% para limitar la velocidad de avance.

\section{Desarrollo Tecnico}
En este capítulo se proporcionará una descripción detallada sobre el funcionamiento de los distintos circuitos que conforman el dispositivo, así como su interacción en conjunto para cumplir con los objetivos del proyecto. Se explicará de manera clara y concisa cómo se utiliza el dispositivo, incluyendo instrucciones específicas para su correcto manejo y operatividad.

Además, se incluirán datos técnicos relevantes, tales como especificaciones de los componentes, características del diseño, y cualquier otro detalle que sea esencial para la comprensión del sistema. También se abordarán aspectos importantes acerca de las partes constitutivas del dispositivo, su función dentro del esquema general, y las consideraciones necesarias para su mantenimiento y optimización.

\subsection{Descripcion del funcionamiento}
El usuario se sienta en la silla de ruedas y se coloca el dispositivo EEG. El EEG capta las señales cerebrales (alfa, beta, gamma, delta y theta) y las somete a un proceso de filtrado por hardware que incluye un filtro notch de 50 Hz, un filtro pasa-bajo de 100 Hz, un filtro pasa-alto de 0,5 Hz y un segundo filtro notch de 50 Hz. Posteriormente, las señales pasan por un circuito de compensación de offset para poder realizar la lectura por parte de la RP2040 Zero ya que la misma no puede leer valores negativos. Esta unidad se encarga de leer los datos mediante cuatro canales de ADC y enviarlos a la Raspberry Pi 4 por protocolo UART, donde se aloja el programa principal para el funcionamiento de la silla de ruedas.

Entre estos códigos se encuentran el control de motores, los filtros digitales, el procesamiento de señales y la inteligencia artificial (IA). Una vez las señales llegan a la Raspberry Pi 4, se filtran digitalmente para eliminar el ruido y mejorar la calidad de los datos. Tras el filtrado, las señales se envían a la IA, que tiene la función de reconocer los patrones cerebrales y determinar la dirección en la que el usuario desea moverse. Una vez el patrón ha sido identificado, se envía una señal a los motores para dirigir la silla hacia la dirección deseada (adelante, atrás, izquierda o derecha).

Además, el proyecto incluye un sistema de emergencia diseñado para garantizar la seguridad del usuario. Este sistema se activa si se detecta un error en la lectura de las señales o si hay un obstáculo en la trayectoria deseada. Su objetivo es prevenir accidentes y aumentar la seguridad del usuario al utilizar la silla de ruedas.

El sistema de emergencia utiliza sensores de ultrasonido para detectar la presencia de objetos a menos de 20 cm de la silla. En caso de detección, el sistema frena los motores y activa un LED en la dirección del objeto, además de un buzzer que emite una señal sonora durante un breve período para alertar al usuario sobre la activación del sistema.

\subsubsection{Funcionamiento del EEG}

\subsubsection{Funcionamiento de los filtros HardWare}

\subsubsection{Funcionamiento de los filtros digitales}

\subsubsection{Funcionamiento del Puente H}

\subsubsection{Funcionamiento del Sistema de Emergencia}

\section{Circuitos usados}
En este capítulo se incluirán imágenes de los esquemas de los circuitos, junto con su representación gráfica en formato virtual de los circuitos impresos, así como fotografías de los circuitos completos una vez finalizados.

\subsubsection{Esquemáticos de los filtros}

\subsubsection{Esquemáticos de los Puentes H}

\begin{figure}[H]
    \centering
     
    \caption{Puente H (Un Motor)}
\end{figure}

\subsubsection{Esquemático del sistema de emergencia}

\begin{figure}[H]
    \centering
    
    \caption{Esquemático del sistema de emegencia}

    \begin{subfigure}[t]{0.5\textwidth}
        \centering
        
        \caption{PCB Del sistema de emergencia}
    \end{subfigure}%
    ~ 
    \begin{subfigure}[t]{0.5\textwidth}
        \centering
        
        \caption{Modelo 3D Del sistema de emergencia}
    \end{subfigure}

\end{figure}

\subsection{Lista de materiales}
Los programas desarrollados para el proyecto, tales como los filtros digitales, sistemas de inteligencia artificial y otros códigos relacionados, se almacenan en los siguientes dispositivos:

\begin{itemize}
    \item Raspberry Pi 4
    \item RP2040-zero
\end{itemize}

\subsubsection{EEG}
\begin{enumerate}
    \item TL084 (x4)
    \item AD620 (x8)
    \item Capacitores 100nF (x48)
    \item Resistencias 100Ω (x4)
    \item Resistencias 120Ω (x16)
    \item Resistencias 560Ω (x8) 
    \item Resistencias 820Ω (x16)
    \item Resistencias 1,5kΩ (x8)
    \item Resistencias 4,7kΩ (x16)
    \item Resistencias 12kΩ (x8)
    \item Resistencias 15kΩ (x8)
    \item Resistencias 27kΩ (x16)
    \item Resistencias 470kΩ (x8)
    \item Resistencias 2,7MΩ (x8)
    \item Electrodos (x9)
\end{enumerate}

\subsubsection{Placa OffSet}
\begin{enumerate}
    \item L7805 (x1)
    \item TL084 (x4)
    \item Jumpers (x2)
    \item Diodos Zenner 3,3V (x4)
    \item Capacitores 100nF (x4)
    \item Resistencias 220Ω (x4)
    \item Resistencias 50kΩ (x8)
    \item Resistencias 100kΩ (x8)
\end{enumerate}

\subsubsection{Sistema de Emergencia}
\begin{enumerate}
    \item Transistor BC546 (x1)
    \item Buzzer 5V (x1)
    \item LEDs Rojos (x4)
    \item Resistencias 220Ω (x4)
    \item Resistencia 4,7kΩ (x1)
\end{enumerate}

\subsubsection{Puentes H}
\begin{enumerate}
    \item Transistores IRF4905 (x4)
    \item Transistores IRF2805 (x4)
    \item Optoacopladores PC817 (x4)
    \item Motores 24V 575W (x2)
    \item Resistencias 100Ω (x4)
    \item Resistencias 180Ω (x4)
    \item Resistrencias 1kΩ (x4)
    \item Resistencias 4,7kΩ (x4)
\end{enumerate}

\subsubsection{Placa reguladora de tensión}
\begin{enumerate}
    \item LM7815 (x1)
    \item Capacitor 100μF (x1)
    \item Capacitor 330μF (x1)
    \item Capacitor 470μF 35V (x1)
    \item Capacitor 470μF 25V (x1)
\end{enumerate}

\section{Conclusiones}
En esta sección se presentará un análisis detallado de los conocimientos adquiridos a lo largo del desarrollo del proyecto, así como las conclusiones a las que hemos llegado durante este proceso. Se incluirán las conclusiones finales obtenidas, así como una evaluación de las principales limitaciones que afectaron el progreso del trabajo. Además, se ofrecerá un resumen de los resultados alcanzados, destacando los aspectos más relevantes y significativos. Finalmente, se abordarán las perspectivas futuras del proyecto, delineando los pasos a seguir para continuar su desarrollo y mejorarlo en el futuro.

\subsection{Resumen de Resultados}

\subsection{Limitaciones}
Durante la ejecución de este proyecto, nos enfrentamos a diversas limitaciones, algunas de las cuales fueron ocasionadas por circunstancias personales de cada integrante del equipo. Como es común en todo proyecto, al principio experimentamos dificultades en la organización y carecíamos de ciertos conocimientos técnicos, los cuales fuimos adquiriendo a lo largo del año.

El tiempo dedicado al proyecto quizá no fue suficiente, considerando la magnitud y la ambición del mismo. Además de estos desafíos iniciales, una de las principales limitaciones fue el prolongado tiempo de espera para obtener los materiales necesarios, los cuales provenían principalmente de la cooperadora. Dado que esta era nuestra principal fuente de herramientas y componentes, nuestro progreso estuvo estrictamente limitado por los tiempos de adquisición manejados por la institución.

Asimismo, al estar creando algo “nuevo”, nos vimos obligados a adoptar un enfoque basado en la prueba y error, ya que la información disponible sobre los temas específicos que requeríamos era escasa. Esta situación también representó un obstáculo significativo, ya que corregir nuestros errores consumió una parte considerable de nuestro tiempo.

Finalmente, al tratarse de un proyecto desarrollado en el ámbito escolar, también nos vimos limitados por el tiempo disponible en la escuela. No pudimos dedicar todo nuestro tiempo al proyecto, ya que debíamos atender otras asignaturas y compromisos académicos.

\subsection{Trabajo Futuro}
El proyecto presenta un alto potencial de rentabilidad en el futuro, sustentado en su carácter innovador y las posibilidades que ofrece su desarrollo continuo. Al tratarse de un invento único en su categoría, se prevé que, con el tiempo y el trabajo adicional necesario, este dispositivo pueda alcanzar un nivel de madurez suficiente para ser comercializado a gran escala.

La inversión en tiempo y recursos adicionales permitirá perfeccionar sus características técnicas, optimizar su funcionalidad, y adaptar el producto a las necesidades de un mercado en expansión. Una vez finalizado y refinado, el proyecto podrá captar la atención de un público más amplio, lo que incrementará su viabilidad comercial y su posicionamiento en el mercado.

En caso de que el desarrollo del proyecto no se complete en su totalidad, este podrá ser aprovechado por la institución educativa, permitiendo que otros grupos de estudiantes continúen su avance. De esta manera, el proyecto no solo servirá como un recurso valioso para futuras generaciones, sino que también fomentará la colaboración y el aprendizaje continuo dentro de la comunidad académica, garantizando su evolución y finalización.
\subsection {Informacion Adicional}
La silla desarrollada en este proyecto es un prototipo, es decir, puede contener fallas de todo tipo, y es sujeto a modificaciones a futuro. Se recomienda su uso siempre acompañado, en zonas amplias libres de obstáculos. No se debe usar en lugares húmedos o si el equipo está mojado, y la inteligencia artificial está adaptada a las muestras de una persona del equipo del proyecto, por lo que para ser usada por alguien mas se deberán muestrear los patrones de movimiento de esta misma.

\subsubsection{Programas Utilizados}
Para el desarrollo del proyecto, hemos requerido hacer uso de los siguientes porogramas, con sus enlaces principales: \newline

    \href{https://github.com/}{-Github}    
    \newline

    \href{https://code.visualstudio.com/}{-Visual Studio Code}
    \newline

    \href{https://thonny.org/}{-Thonny}
    \newline

    \href{https://es.overleaf.com/project}{-Overleaf}
    \newline

    \href{https://www.jetbrains.com/es-es/pycharm/}{-Pycharm}
    \newline

    \href{https://termius.com/}{-Termius}
    \newline

    \href{https://www.kicad.org/}{-Kicad}
    \newline

    \href{https://livewire.laravel.com/}{-Livewire}
    \newline

    \href{https://www.analog.com/en/resources/design-tools-and-calculators/ltspice-simulator.html}{-LTSpice}
    \newline

    \href{https://github.com/apps/desktop}{-GitHub Desktop}

\subsubsection{Agradecimientos}

Queremos expresar nuestro más profundo agradecimiento a los profesores que nos han brindado su invaluable apoyo en la realización de este proyecto:

Fabrizio Carlassara: Su asistencia fue crucial en la programación de la mayor parte del proyecto, así como en la creación de circuitos y esquemáticos, la búsqueda de materiales y el desarrollo de los filtros necesarios.

Sergio Medina: Nos brindó su experiencia en la presentación y comercialización del proyecto, además de colaborar en la programación, la búsqueda de materiales y la planificación de los puentes H.

Carlos Bianco: Su apoyo fue esencial en las pruebas y acondicionamiento de los motores, proporcionándonos herramientas y baterías para dichas pruebas, además de colaborar en la búsqueda de materiales.

Daniel Espósito: Nos proporcionó motores y materiales, además de enseñarnos a construir los puentes H para los motores, facilitando su creación y optimización.

Federico Solomiewicz: Su colaboración fue invaluable en el desarrollo de los filtros, proporcionándonos herramientas para el proyecto y estando siempre disponible para resolver cualquier duda que surgiera.

Juan Carlos Ruiz: Su colaboración fue esencial en las pruebas de los motores para la silla de ruedas, adempas de ayudarnos principalmente en la creación de los puentes H para los motores y sus circuitos impresos.

\section{Referencias}
En este apartado se presentarán de manera detallada las referencias consultadas al inicio del proyecto, las cuales fueron fundamentales para la conceptualización y desarrollo de la idea final. Estas fuentes proporcionaron el marco teórico y práctico necesario para orientar la dirección del trabajo, influyendo en las decisiones tomadas durante el proceso de diseño y ejecución.
\subsubsection{Autodesk Instructables}
A partir de esta página, obtuvimos los primeros circuitos necesarios para el EEG, lo que nos permitió avanzar de manera significativa en el desarrollo del proyecto. Esta fuente de información fue fundamental para sentar las bases técnicas y nos brindó las herramientas necesarias para continuar con el diseño y la implementación del sistema.

\section{Lista de códigos}

\subsection{Códigos principales}

\subsubsection{bias.py}
\lstinputlisting[language=python]{Codigos/CodigosPrincipales/bias.py}

\subsubsection{app.py}

\subsection{Inteligencia artificial}

\subsubsection{bias\_ai.py}

\subsection{Filtrado y procesamiento de señales}

\subsubsection{bias\_dsp.py}

\subsubsection{bias\_graphing.py} 
\lstinputlisting[language=python]{Codigos/Filtrado/bias_graphing.py}

\subsection{Motores}

\subsubsection{bias\_motors.py}
\lstinputlisting[language=python]{Codigos/Motores/bias_motors.py}

\subsection{Recepción de señales}

\subsubsection{bias\_reception.py}
\lstinputlisting[language=python]{Codigos/Recepcion/bias_reception.py}

\subsubsection{CMakeLists.txt}

\subsubsection{pico\_sdk\_import.cmake}

\subsubsection{reception.c}

\subsection{Página Web}
El sitio web ofrece una breve descripción sobre nosotros, nuestros objetivos, y proporciona enlaces a nuestras redes sociales, donde podrán contactarnos o conocer más acerca de nuestro trabajo.

\begin{center}
    \href{https://proyectobias.github.io/Bias/}{Página Web}
\end{center}

\subsubsection{Lenguaje utilizado en la página web y su código}
El desarrollo de la página web se realizó utilizando los lenguajes HTML y CSS.

Aquí se adjuntan los códigos de la página web:

\begin{center}
    Index.css
\end{center}

\lstinputlisting[language=CSS]{PaginaWeb/index.css}

\begin{center}
    Index.html
\end{center}

\lstinputlisting[language=html]{PaginaWeb/index.html}

\end{document}

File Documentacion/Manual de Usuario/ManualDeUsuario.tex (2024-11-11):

\documentclass{article} 
\UseRawInputEncoding
\usepackage[utf8]{inputenc}
\usepackage[T1]{fontenc}
\usepackage{selinput}
\usepackage[spanish]{babel}
\usepackage{hyphenat}
\usepackage{graphicx} 
\usepackage{subcaption}
\usepackage{hyperref}
\usepackage{listings}
\usepackage{multicol}
\usepackage{xcolor}
\usepackage{float}
\usepackage{array}
\usepackage[a4paper, total={6in, 9in}]{geometry}
\SelectInputMappings{%
  eacute={é},
}

\definecolor{codegreen}{rgb}{0,0.6,0}
\definecolor{codegray}{rgb}{0.5,0.5,0.5}
\definecolor{codepurple}{rgb}{0.58,0,0.82}
\definecolor{backcolour}{rgb}{0.95,0.95,0.92}

\lstdefinestyle{mystyle}{
    backgroundcolor=\color{backcolour},
    commentstyle=\color{codegreen},
    keywordstyle=\color{blue},
    numberstyle=\tiny\color{codegray},
    stringstyle=\color{codepurple},
    basicstyle=\ttfamily\footnotesize,
    breakatwhitespace=false,
    breaklines=true,
    captionpos=b,
    keepspaces=true,
    numbers=left,
    numbersep=5pt,
    showspaces=false,
    showstringspaces=false,
    showtabs=false,
    tabsize=2
}

\lstdefinelanguage{CSS}{
  keywords={color,background-image:,margin,padding,font,weight,display,position,top,left,right,bottom,list,style,border,size,white,space,min,width, transition:, transform:, transition-property, transition-duration, transition-timing-function},	
  sensitive=true,
  morecomment=[l]{//},
  morecomment=[s]{/*}{*/},
  morestring=[b]',
  morestring=[b]",
  alsoletter={:},
  alsodigit={-}
}
\lstset{style=mystyle}

\title{Manual de Usuario} 

\date{} 

\begin{document} 

\begin{figure}[H]
    \centering
    
\end{figure}

\tableofcontents

\newpage

\section{Introduccion}
Bienvenido/a

Gracias por elegir nuestra silla de ruedas controlada mediante señales cerebrales. Este manual le guiará en los pasos para el correcto uso y la colocación de los electrodos de forma segura y efectiva.

\section{Precauciones Generales}
\begin{itemize}
    \item Use el dispositivo en un entorno controlado y seguro.
    \item Verifique que todos los componentes estén en buen estado antes de cada uso.
    \item No intente modificar el equipo.
\end{itemize}

\section{Descripcion del Sistema}
Este sistema utiliza un EEG de 9 electrodos que detectan señales cerebrales para controlar la dirección de la silla de ruedas. El dispositivo incluye un sistema de emergencia que se activa al detectar obstáculos.

\section{Instrucciones de Preparacion}
\subsection{Colocacion de Electrodos}
\begin{enumerate}
    \item \textbf{Preparación de la Piel}
    \begin{itemize}
        \item Limpie el cuero cabelludo para eliminar aceites y residuos.
        \item Aplique una pequeña cantidad de pasta conductora en cada electrodo para luego colocarlo sobre el cuero cabelludo (asegurese de mover el pelo para que el electrodo toque la mayor cantidad de piel posible).
    \end{itemize}
    \item \textbf{Posicionamiento de los Electrodos (Sistema 10-20):}
    \begin{itemize}
        \item \textbf{Electrodo de Tierra:} Coloque el electrodo de referencia (electrodo de color verde) en el lobulo de la oreja.
        \item Electrodos de Señal:
        \begin{itemize}
            \item Coloque los electrodos de acuerdo a los puntos específicos designados en el EEG. Estos puntos son:
            
            Para los electrodos positivos (electrodos de color rojo): C3, C4, Cz y Fc3
            
            Para los electrodos negativos (electrodos de color negro): Fc1, Fc2, Pz, Fc4
            \item Asegure cada electrodo en su lugar sin que queden sueltos, para obtener una lectura de señal estable.
        \end{itemize}
    \end{itemize}
    \item \textbf{Revisión Final}
    \begin{itemize}
        \item Verifique que todos los electrodos estén bien conectados y que el sistema esté ajustado pero cómodo.
    \end{itemize}
    
\end{enumerate}

\section{Uso de la Silla de Ruedas}
\subsection{Encendido del Sistema}
\begin{enumerate}
    \item Encienda la silla de ruedas y el EEG presionando los botones de encendido en ambos dispositivos.
    \item Espere unos segundos mientras el sistema realiza las calibraciones iniciales.
\end{enumerate}

\subsection{Control de Movimientos}
Relájese y concéntrese en pensar en los parametros de la siguiente tabla para poder moverse en la direccion deseada:
\\
\\
\begin{table}[H]
    \renewcommand{\arraystretch}{1.5}
    \centering
    \begin{tabular}{|p{4cm}|p{4cm}|}
        \hline
        Movimiento a Pensar & Direccion hacia donde se mueve la silla \\
        \hline
        Pies & Adelante \\
        \hline
        Lengua & Atras \\
        \hline
        Mano izquierda & Izquierda \\
        \hline
        Mano derecha & Derecha \\
        \hline
    \end{tabular}
\end{table}
El sistema traducirá las señales cerebrales en movimiento hacia adelante, atrás, izquierda o derecha.

\subsection{Sistema de Emergencia}
\begin{enumerate}
    \item En caso de detectar un obstáculo, la silla de ruedas se detendrá automáticamente.
    \item Un indicador sonoro y visual (buzzer y LED) se activará si un obstáculo impide el movimiento en la dirección deseada.
    \item A los lados, al frente y atras de la silla se encuentran los ultrasonidos. Antes de usar la silla, asegurese que estos no esten tapados.
\end{enumerate}

\section{Mantenimiento y Cuidado}
\begin{itemize}
    \item Limpie los electrodos y las bandas regularmente.
    \item Revise la carga de la batería del EEG y de la silla.
    \item Si la bateria del EEG esta agotada, puede cambiarla por 2 baterias de 9V y poner a cargar las otras 2 agotadas.
    \item Si la bateria del motor esta agotada, debe cambiarse la bateria por otra de 24V y 36 Amph y poner a cargar la anterior en una estacion especializada.
\end{itemize}

\section{Solucion de Problemas}

\begin{table}[H]
    \renewcommand{\arraystretch}{1.5}
    \centering
    \begin{tabular}{|p{4cm}|p{4cm}|p{4cm}|}
        \hline
        Problema & Posible Causa & Solucion \\
        \hline
        La silla no responde & Conexion inadecuada del EEG & Verifique los electrodos \\
        \hline
        Señal de EEG inestable & Electrodos mal conectados & Asegure y ajuste los electrodos \\
        \hline
        Sistema de Emergencia se activa sin razon & Obstruccion o interferencia en sensores & Limpie o revise el area de los sensores \\
        \hline
    \end{tabular}
\end{table}
\textbf{Contacte al servicio técnico} en caso de problemas recurrentes.

\section{Preguntas Frecuentes (FAQ)}
\begin{enumerate}
    \item \textbf{¿Qué debo hacer antes de empezar a usar la silla de ruedas?}
    \begin{itemize}
        \item Asegúrese de que la batería de la silla de ruedas esté completamente cargada.
        \item Coloque correctamente los electrodos en las posiciones indicadas. Estos deben estar en buen contacto con el cuero cabelludo para una señal precisa.
        \item Verifique que todos los componentes estén en funcionamiento, como la Raspberry Pi, el EEG y el sistema de emergencia de sensores ultrasónicos.
    \end{itemize}
    \item \textbf{¿Cómo debo colocar los electrodos correctamente?}
    
    Coloque los electrodos en el cuero cabelludo siguiendo las instrucciones del manual. Asegúrese de que estén bien ajustados y en contacto firme. Puede consultar la sección de "Colocación de Electrodos" para una guía detallada.
    \item \textbf{¿Cómo se controla la dirección de la silla de ruedas?}
    
    La silla utiliza un sistema de inteligencia artificial que interpreta patrones específicos de las señales cerebrales para determinar la dirección: adelante, atrás, izquierda o derecha. Es importante estar relajado y enfocado en la dirección que desea.
    \item \textbf{¿Qué sucede si se detecta un obstáculo en el camino de la silla?}
    
    El sistema de emergencia activará los sensores ultrasónicos, y si detecta un obstáculo en la dirección de movimiento, encenderá un LED y activará el buzzer para advertirle y detener el movimiento.
    \item \textbf{¿Puedo usar la silla de ruedas en exteriores?}
    
    Sí, la silla puede utilizarse en exteriores, pero debe evitarse su uso en entornos donde los sensores ultrasónicos puedan no funcionar adecuadamente, como superficies irregulares o áreas con mucha interferencia electromagnética.
    \item \textbf{¿Qué debo hacer si la silla de ruedas no responde a los comandos mentales?}
    \begin{itemize}
        \item Asegúrese de que los electrodos estén bien conectados y que haya un buen contacto con el cuero cabelludo.
        \item Verifique que la batería de la Raspberry Pi y del EEG estén cargadas.
        \item Reinicie el sistema si persiste el problema.
    \end{itemize}
    \item \textbf{¿Cuánto dura la batería y cómo la recargo?}
    
    La duración de la batería puede variar según el uso, pero generalmente dura unas pocas horas.
    \item \textbf{¿Qué hago si necesito ayuda para el uso del dispositivo?}
    
    Si tiene alguna duda adicional o problema técnico, consulte la sección de Recursos Adicionales en el manual o contacte al equipo de soporte utilizando el número o correo electrónico proporcionado en la última página del manual.
    \item \textbf{¿Se necesita un entrenamiento especial para usar esta silla de ruedas?}
    
    Sí bien no es necesario, es recomendable que el usuario pase por una sesión de entrenamiento breve para aprender a controlar la silla con las señales cerebrales. Esto ayuda a familiarizarse con el proceso de enfoque y control de la dirección.
    \item \textbf{¿Qué debo hacer si se presenta una falla en el sistema?}
    
    Apague la silla de ruedas y desconecte la batería si es seguro hacerlo. Luego, revise la sección de "Solución de Problemas" en el manual. Si el problema persiste, póngase en contacto con el servicio técnico.
\end{enumerate}
\newpage

\section{Recursos Adicionales}
\begin{multicols}{2}

    \subsection{Integrantes} 
    \begin{itemize}
        \item Adell, Nicolas Fabian 
        \item De Blasi, Luca 
        \item Diaz Melion, Danilo Sebastian 
        \item Gil Soria, Ian Lucas 
        \item Montenegro, Luciano Nahuel 
        \item Sojka, Santiago Alejandro 
    \end{itemize}
    
    \subsection{Soporte Técnico} 
    \begin{itemize}
        \item \textbf{Telefono:}
        
        +54 9 11 6939-8053
        \item \textbf{Correo Electronico:}
        
        bias.project.impa@gmail.com
    \end{itemize}
    
    \columnbreak
    
    \subsection{Actualizaciones y Descargas} 
    Consulta la página de descargas en nuestro sitio web para obtener actualizaciones de software y mejoras del sistema: 

    \texttt {https://sojkaa.github.io/BIAS-WEB/}
    
    \subsection{Comunidad en Linea}
    \textbf{Redes Sociales} 
    
    \texttt{https://linktr.ee/biasproject} 
    
    \textbf{GitHub} 
    
    \texttt{https://github.com/impatrq/bias} 
    
    \textbf{Trello} 
    
    \texttt{https://trello.com/w/2024_722c_bias} 

\end{multicols}

\end{document}

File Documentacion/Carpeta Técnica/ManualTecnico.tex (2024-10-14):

\documentclass{article} 
\UseRawInputEncoding
\usepackage[utf8]{inputenc}
\usepackage[T1]{fontenc}
\usepackage{selinput}
\usepackage[spanish]{babel}
\usepackage{hyphenat}
\usepackage{graphicx} 
\usepackage{subcaption}
\usepackage{hyperref}
\usepackage{listings}
\usepackage{xcolor}
\usepackage{float}
\usepackage[a4paper, total={6in, 9in}]{geometry}
\SelectInputMappings{%
  eacute={é},
}

\definecolor{codegreen}{rgb}{0,0.6,0}
\definecolor{codegray}{rgb}{0.5,0.5,0.5}
\definecolor{codepurple}{rgb}{0.58,0,0.82}
\definecolor{backcolour}{rgb}{0.95,0.95,0.92}

\lstdefinestyle{mystyle}{
    backgroundcolor=\color{backcolour},
    commentstyle=\color{codegreen},
    keywordstyle=\color{blue},
    numberstyle=\tiny\color{codegray},
    stringstyle=\color{codepurple},
    basicstyle=\ttfamily\footnotesize,
    breakatwhitespace=false,
    breaklines=true,
    captionpos=b,
    keepspaces=true,
    numbers=left,
    numbersep=5pt,
    showspaces=false,
    showstringspaces=false,
    showtabs=false,
    tabsize=2
}

\lstdefinelanguage{CSS}{
  keywords={color,background-image:,margin,padding,font,weight,display,position,top,left,right,bottom,list,style,border,size,white,space,min,width, transition:, transform:, transition-property, transition-duration, transition-timing-function},	
  sensitive=true,
  morecomment=[l]{//},
  morecomment=[s]{/*}{*/},
  morestring=[b]',
  morestring=[b]",
  alsoletter={:},
  alsodigit={-}
}
\lstset{style=mystyle}
\date{} 

\begin{document} 

\begin{center}
    \\ 
\end{center}
    
\title{BIAS} 

\vspace{1cm} 

\textbf{Integrantes del Proyecto:} 

\begin{itemize}
    \item Adell, Nicolas Fabian
    \item De Blasi, Luca
    \item Diaz Melion, Danilo Sebastian
    \item Gil Soria, Ian Lucas
    \item Montenegro, Luciano Nahuel
    \item Sojka, Santiago Alejandro
\end{itemize}

\tableofcontents 

\newpage 

\section{Introducción}

BIAS es un módulo aplicable a una silla de ruedas que permite a los usuarios dirigirla mediante sus pensamientos, eliminando la necesidad de controles físicos tradicionales y optimizando la experiencia de movilidad. Este proyecto representa un avance significativo en el campo de la movilidad asistida, con el objetivo de mejorar la independencia y la calidad de vida de las personas con movilidad reducida.

Este sistema se basa en la avanzada tecnología de interfaz cerebro-computadora (BCI), la cual captura las señales neuronales del usuario y las traduce en comandos precisos para maniobrar la silla de ruedas sin esfuerzo. Además, el diseño modular y adaptable del sistema permite su integración en diversos modelos de sillas de ruedas y su personalización según las necesidades específicas de cada usuario. 

La seguridad es una prioridad fundamental en este desarrollo, por lo que el módulo incorpora múltiples capas de redundancia y verificación de señales, asegurando que la silla de ruedas responda de manera precisa y confiable a las intenciones del usuario. 

Aspiramos a revolucionar la forma en que las personas con movilidad reducida interactúan con su entorno, brindándoles una herramienta que amplía su capacidad para controlar su vida de manera más segura e independiente.

\subsection{Resumen del proyecto}
Este proyecto se centra en el desarrollo de una silla de ruedas controlada mediante señales cerebrales. El sistema se compone principalmente de los siguientes componentes: la silla de ruedas, un dispositivo EEG (electroencefalografo) y dos motores que permiten al usuario moverse en la dirección deseada.

El funcionamiento del sistema es el siguiente: el usuario se sienta en la silla y se coloca el EEG en la cabeza. A continuación, el usuario piensa en mover la lengua, las manos y los pies (mano izquierda, moviemiento a la izquierda, mano derecha, movimiento a la derecha, la lengua es hacia atras y los pies es hacia adelante).  en la que desea moverse, y los motores responden en consecuencia.

El EEG tiene la función de leer las señales cerebrales del usuario. Estas señales se clasifican en las categorías de alpha, beta, gamma, delta y theta, y luego se someten a un proceso de filtrado para eliminar cualquier ruido. Posteriormente, las señales filtradas son analizadas por una Inteligencia Artificial (IA) desarrollada por nuestro equipo, la cual identifica patrones para determinar si el usuario desea moverse o detenerse.

Además, la silla está equipada con un sistema de emergencia que se activa en caso de lecturas erróneas o la detección de obstáculos. Este sistema de emergencia está compuesto por ultrasónidos que detectan la presencia de obstáculos frente a la silla.

\subsection{Motivación}
Como estudiantes de séptimo año, buscamos desarrollar un proyecto con el fin de cumplir con el requerimiento horario de practicas profesionalizantes. Nuestra intención inicial fue encontrar el proyecto ideal en cuestiones de impacto social, enfocándonos en la mejora de la calidad de vida de aquellas personas con discapacidades. Bajo este marco, y tras una extensa investigación, proponemos crear un módulo aplicable a una silla de ruedas controlado mediante la actividad cerebral del usuario, utilizando tecnología de interfaces cerebro-computadora (BCI), para brindarles mayor autonomía, independencia y participación social.   Creemos que este proyecto tiene el potencial de transformar la vida de las personas con movilidad motora reducida debido a enfermedades como ELA, esclerosis múltiple o cuadriplejia, permitiéndoles controlar su propio movimiento y mejorar significativamente su calidad de vida.
\subsection{Objetivos}
El objetivo de este proyecto es desarrollar una silla de ruedas motorizada que pueda ser controlada por la actividad cerebral del usuario. Esto beneficiaría a las personas con discapacidades motoras severas para lograr independencia y movilidad, mejorando su calidad de vida y participación en la sociedad. De esta manera, estas personas las cuales no pueden caminar o tienen movilidad reducida, pueden gozar de la utilización de una silla de ruedas controlada por señales cerebrales sin la utilización de ambas manos y meramente por sus pensamientos, dándole libertad y autonomía al usuario.

\section{¿Quiénes somos?}
Somos el grupo BIAS (Brain Intelligence Artificial System), conformado por seis estudiantes de la especialidad de Aviónica del séptimo año, segunda división, comisión C, de la Escuela Técnica N° 7 IMPA "Taller Regional Quilmes". Nuestro equipo se encuentra comprometido en el desarrollo de un módulo adaptable para sillas de ruedas, para así poder brindarles mas independencia y movilidad.
\subsection{Contactos}

En este apartado se detallarán los contactos a los integrantes del proyecto, adjuntando enlaces a sus redes:

\subsubsection{Adell Nicolás}

\begin{minipage}[t]{0.3\textwidth}
\begin{figure}[H]
    
\end{figure}
\end{minipage}
\begin{minipage}[t]{0.5\textwidth}
    \vspace{3.5em}
    \href{https://instagram.com/nicolas.adell}{Instagram} \\[1em]
    \href{http://www.linkedin.com/in/nicolas-adell-354508297}{LinkedIn} \\[1em]
    \href{mailto:nicolas.fabian2005@gmail.com}{Gmail}
\end{minipage}%

\subsubsection{De Blasi Luca}

\begin{minipage}[t]{0.3\textwidth}

\begin{figure}[H]
    
\end{figure}

\end{minipage}
\begin{minipage}[t]{0.5\textwidth}
    \vspace{3.5em}
    \href{https://instagram.com/luca.deblasii}{Instagram} \\[1em]
    \href{https://www.linkedin.com/in/luca-de-blasi-31164b304}{LinkedIn} \\[1em]
    \href{mailto:luqac2006@gmail.com}{Gmail}
\end{minipage}%

\subsubsection{Diaz Melión Danilo}

\begin{minipage}[t]{0.3\textwidth}

    \begin{figure}[H]
        
    \end{figure}

\end{minipage}
\begin{minipage}[t]{0.5\textwidth}
    \vspace{3.5em}
    \href{https://instagram.com/_danilodiaz}{Instagram} \\[1em]
    \href{https://www.linkedin.com/in/danilodiazmelion/}{LinkedIn} \\[1em]
    \href{mailto:danilodiaz934@gmail.com}{Gmail}
\end{minipage}%

\subsubsection{Gil Soria Ian}
\begin{minipage}[t]{0.3\textwidth}

\begin{figure}[H]
    
\end{figure}

\end{minipage}
\begin{minipage}[t]{0.5\textwidth}
    \vspace{3.5em}
    \href{https://instagram.com/ian_gilsooor}{Instagram} \\[1em]
     \href{https://www.linkedin.com/in/ian-lucas-gil-soria-a8090b2a8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}{LinkedIn} \\[1em]
    \href{mailto:ianlucasgilsoria@gmail.com}{Gmail}
\end{minipage}%

\subsubsection{Montenegro Luciano}
\begin{minipage}[t]{0.3\textwidth}

\begin{figure}[H]
    
\end{figure}

\end{minipage}
\begin{minipage}[t]{0.5\textwidth}
    \vspace{3.5em}
    \href{https://instagram.com/luchito_.montenegro}{Instagram} \\[1em]
    \href{https://www.linkedin.com/in/luciano-montenegro-3215aa304}{LinkedIn} \\[1em]
    \href{mailto:lucianomontenegro1021@gmail.com}{Gmail}
\end{minipage}%

\subsubsection{Sojka Santiago}
\begin{minipage}[t]{0.3\textwidth}
\begin{figure}[H]
    
\end{figure}
\end{minipage}
\begin{minipage}[t]{0.5\textwidth}
    \vspace{3.5em}
    \href{https://instagram.com/sojkaa.sant}{Instagram} \\[1em]
    \href{https://www.linkedin.com/in/santiago-sojka-817198271/}{LinkedIn} \\[1em]
    \href{mailto:santiagosojka@gmail.com}{Gmail}
\end{minipage}%

\section{Desarrollo del Proyecto}
En este capítulo se expondrá en detalle la metodología empleada para avanzar en el desarrollo del proyecto, incluyendo las fuentes de inspiración y los proyectos similares que se tomaron como referencia para el diseño de nuestros circuitos y la programación de los sistemas. Además, se incluirán imágenes ilustrativas de estos proyectos de referencia, con el fin de ofrecer una comprensión visual más completa. Al finalizar el capítulo, se presentarán y explicarán los resultados obtenidos, evaluando su eficacia en relación con los objetivos planteados.

\subsection{Metodología}
La metodología aplicada en este proyecto se basa en la organización del equipo en dos grupos especializados. El primer grupo se encarga del desarrollo de los programas, siendo ejemplos de esto los filtros virtuales, programas de recepción y procesado, mientras que el segundo se dedica a la implementación de los motores, sistemas de emergencia y filtros. Esta división del trabajo permite una utilización más eficiente del tiempo, al abordar simultáneamente diversas áreas del proyecto, lo que resulta en un avance más significativo en periodos de tiempo más reducidos.

\subsection{Historia del Arte}
En este capitulo se repasa todos los conceptos previamente vistos mediante los cuales pudimos empezar a conceptualizar la idea del proyecto.

\subsubsection{Neuralink}
Uno de los casos que nos permitió aproximarnos a la conceptualización del proyecto fue el chip cerebral estilo implante de Neuralink, denominado Telepathy. Este dispositivo, desarrollado por la compañía de Elon Musk, tiene como objetivo facilitar la vida de las personas mediante la optimización de herramientas y su adaptación al cuerpo humano a través del implante. El chip crea una conexión entre el ser humano y dispositivos electrónicos, permitiendo, por ejemplo, controlar una puerta con traba eléctrica, desbloquear un teléfono móvil, e incluso monitorear el estado de ánimo de las personas.

Este ejemplo nos ofreció una perspectiva sobre la viabilidad de desarrollar un dispositivo, que, aunque no tan complejo, pudiera ser controlado por el propio cuerpo humano. A partir de esta premisa, iniciamos una investigación para explorar las posibilidades y opciones disponibles basadas en esta idea.

\subsubsection{Ryan Lopez EEG}
Si bien nuestro motivo y objetivo principal era crear un dispositivo original e innovador, también nos propusimos investigar proyectos con cierta similitud. En este proceso, encontramos el repositorio de un estudiante que desarrolló un sistema capaz de detectar señales alfa y, en función de las reacciones o pensamientos del usuario, permitir el control a través de un test de concentración. Este test consistía en que el usuario debía mantener un estado de concentración mientras estudiaba un documento para un examen, en lo que se podría considerar un simulacro.

El sistema desarrollado por Ryanlopezz activaba una alarma si los niveles de concentración del usuario comenzaban a disminuir, basándose en un espectro de señales alfa transmitidas por un conjunto de electrodos EEG dorados conectados a la cabeza del estudiante. Además, el sistema realizaba otras dos pruebas: una de ellas consistía en escribir en código Morse mediante pensamientos, enviando "pulsos de concentración", y la otra permitía controlar el movimiento de un personaje en el famoso videojuego "Flappy Bird", ajustando el impulso para subir o bajar.

En el siguiente link se adjunta la página de GitHub de Ryan Lopez en donde se puede observar más a detalle los programas y archivos de su EEG.

\begin{center}
    \href{https://github.com/ryanlopezzzz/EEG}{Ryan Lopez GitHub}
\end{center}

Gracias al mismo proyecto realizado por este usuario, pudimos desarrollar nuestro propio circuito para el sistema de filtrado, ya que íbamos a requerir otras especificaciones con diferentes funciones, tales como la entrada de señal: ya que esta debía ser mayor a la designada, al nosotros trabajar no solo con el espectro radioelectrico de las señales Alpha, sino con las principales señales que el cerebro produce al momento de realizar un pensamiento especifico; Por otro lado nosotros íbamos a requerir no solo un sistema de filtros EEG sino 4 placas del mismo circuito, debido a la posibilidad de maniobrar controlando los 3 ejes de los motores de la silla de ruedas

\begin{center}
    \\
\end{center}

Por otro lado nos dio una primera vista de la localización de los botones EEG como irían colocados en la cabeza:

\begin{center}
    \\

\end{center}

Así mismo para el estudio del aérea de medicina y saber como el cerebro humano se encarga de transmitir ciertas señales eléctricas gracias a la actividad cerebral  tuvimos en cuenta los actuales dispositivos de eneflografos, como se componen y actúan gracias ala actividad cerebral, bajo un especto radioelectrico determinado adjunto a la clasificación de las ondas transmitidas por el cerebro humano

\subsubsection{OpenBCI}

En nuestra búsqueda de conexiones para un microcontrolador y formas de desarrollar nuestro propio proyecto, descubrimos un sitio web llamado OpenBCI, una compañía especializada en la creación de dispositivos que integran tecnología con la interfaz del cuerpo humano. Esta empresa ha desarrollado un encefalógrafo casero, proporcionando dimensiones y parámetros estructurales que nos permitieron diseñar nuestra propia vincha/casco. Este dispositivo incorpora electrodos EEG, adaptados a la cabeza del usuario, como parte fundamental de nuestro proyecto "BIAS".

\begin{center}
    \\
\end{center}

Además, al ser una compañía especializada en la creación de módulos de microcontroladores, nos proporcionaron orientación en cuanto a cómo realizar las conexiones entre la Raspberry Pi 4 que utilizamos y el sistema de filtrado EEG.

En los siguientes textos se adjuntan enlaces para ver la página oficial de OpenBCI y documentación de referencia correspondiente.

\begin{center}
    \href{https://openbci.com/}{Página oficial de OpenBCI}

    \href{https://docs.openbci.com/}{Documentación}

\end{center}

\begin{figure}[h!]
\centering

\begin{subfigure}[b]{0.45\linewidth}
    
    \caption{Diseño Esquemático}
    \label{fig:westminster_lateral}
\end{subfigure}

\begin{subfigure}[b]{0.45\linewidth}

\caption{Diseño PCB}
\label{fig:westminster_aerea}

\end{subfigure}
\caption{Diseño de microcontrolador de Open BCI}
\label{fig:westminster}
\end{figure}

\begin{center}
    \\

    \\
\end {center}

\subsubsection{Autodesk Instructables}
A partir de esta página, obtuvimos los primeros circuitos necesarios para el EEG, lo que nos permitió avanzar de manera significativa en el desarrollo del proyecto. Esta fuente de información fue fundamental para sentar las bases técnicas y nos brindó las herramientas necesarias para continuar con el diseño y la implementación del sistema.

\section{Desarrollo Teórico}
En este capítulo se describirán y desarrollarán todos los aspectos teóricos relacionados, justificando la elección de los componentes utilizados. Se abordarán teorías como la Jaula de Faraday y el sistema 10-20, además de ofrecer una explicación detallada sobre los tipos de señales empleadas, entre otros temas relevantes.

\subsection{Distinción de alimentaciones}

En la etapa de recepción de señales provenientes de los electrodos, se empleará una fuente de alimentación compuesta por baterías de 9 voltios. La elección de este tipo de alimentación responde a la necesidad de limitar la corriente en caso de que ocurra algún problema en el circuito, previniendo así posibles daños a los componentes electrónicos. Esta misma fuente de alimentación será utilizada para suministrar energía a la placa de offset, asegurando que todos los subsistemas relacionados con la recepción de señales operen bajo condiciones controladas y seguras.

Para la alimentación del microcontrolador RP2040 Zero, se utilizará un regulador de 5 voltios que se encargará de convertir el voltaje de 9 voltios a un nivel más adecuado de 5 voltios, garantizando el correcto funcionamiento del dispositivo. La estabilidad en el suministro de voltaje es crucial en este tipo de sistemas, ya que cualquier fluctuación podría interferir con el procesamiento de las señales cerebrales y comprometer la precisión del sistema de control. Además, las distintas fuentes de alimentación están equipadas con condensadores conectados entre el terminal positivo y GND (tierra), con el objetivo de reducir las fluctuaciones en la tensión y minimizar la introducción de ruido en las señales. El ruido eléctrico, especialmente en sistemas de control y medición sensibles, puede degradar significativamente el rendimiento y la fiabilidad de los datos procesados.

El sistema de control de la silla de ruedas se alimentará mediante una batería de 24 voltios, la cual también suministrará energía al puente H y a los motores responsables del movimiento. Para garantizar la separación adecuada entre las distintas partes del sistema, se utilizará una masa adicional junto con un optoacoplador, que permitirá aislar eléctricamente la etapa de control de la etapa de potencia. Este desacoplamiento es esencial para evitar interferencias entre las señales de control y las corrientes más elevadas que circulan en el circuito de potencia.

Dentro del sistema de control, la Raspberry Pi 4 será alimentada mediante un regulador de 15 voltios, seguido de un segundo regulador que reducirá la tensión a 5 voltios. Este enfoque escalonado para la regulación del voltaje permite una mayor estabilidad en el suministro de energía, mejorando la eficiencia del sistema. De igual manera, se emplearán condensadores conectados en paralelo para reducir las posibles fluctuaciones de tensión y evitar la introducción de ruido, asegurando que la Raspberry Pi 4 funcione de manera óptima. La reducción del ruido es particularmente importante en sistemas basados en señales cerebrales, donde incluso pequeñas perturbaciones pueden alterar los resultados del procesamiento de señales EEG.

Finalmente, el puente H recibirá la alimentación directamente de la batería de 24 voltios. Para mantener una separación adecuada entre la etapa de control y la etapa de alimentación de los motores, se integrará otro optoacoplador, que garantizará que ambas secciones del circuito permanezcan eléctricamente aisladas. Sin embargo, aunque las masas de ambos sistemas no están directamente vinculadas en la placa, comparten el mismo punto de conexión en el borne de la batería de 24 voltios. Este diseño asegura que las distintas partes del sistema mantengan un nivel adecuado de aislamiento, mientras que las conexiones necesarias para la correcta operación del circuito se mantienen intactas.

\subsection{¿Que es un electroencefalograma?}

Un electroencefalograma (EEG) es una prueba médica que registra la actividad eléctrica del cerebro. Esta actividad se mide a través de electrodos colocados en el cuero cabelludo, que detectan las señales eléctricas generadas por las neuronas mientras se comunican entre sí. Estas señales eléctricas se representan como ondas cerebrales en una gráfica que muestra diferentes frecuencias y patrones.

El EEG se utiliza comúnmente para:
\begin{itemize}
    \item \textbf{Diagnóstico de trastornos neurológicos:} Como la epilepsia, convulsiones, trastornos del sueño, encefalopatías o daño cerebral.
    \item \textbf{Monitoreo del estado cerebral:} En procedimientos quirúrgicos, cuidados intensivos o investigaciones sobre coma y muerte cerebral.
    \item \textbf{Investigación neurológica y cognitiva:} Para estudiar la actividad cerebral en respuesta a estímulos externos, emociones o en procesos de toma de decisiones.
    \item \textbf{Interfaz cerebro-computadora (BCI):} Donde se usa para traducir la actividad cerebral en comandos para controlar dispositivos externos, como en tu proyecto de silla de ruedas controlada por EEG.
    
\end{itemize}

Las ondas cerebrales se clasifican en varios tipos según su frecuencia: delta, theta, alpha, beta, y gamma, cada una asociada a diferentes estados de conciencia y actividades cerebrales.

\begin{figure}[H]
    \centering
    
    \caption{Vision de las Ondas Cerebrales en un electroencefalograma}
    \label{fig:enter-label}
\end{figure}

\subsection{¿Que es un EEG?}
Un electroencefalógrafo (EEG) es un dispositivo médico que se utiliza para registrar y medir la actividad eléctrica del cerebro. Su función principal es captar las señales eléctricas generadas por las neuronas y transformarlas en gráficos de ondas cerebrales, que se pueden analizar para evaluar la función cerebral, diagnosticar trastornos neurológicos y estudiar patrones de actividad cerebral. Las aplicaciones de los EEG incluyen investigaciones científicas, monitoreo clínico en neurocirugía, diagnóstico de epilepsia y el desarrollo de interfaces cerebro-computadora (BCI), como el control de dispositivos a través de señales cerebrales.

\subsubsection{Componentes que tiene un EEG:}
\begin{itemize}
    \item \textbf{Electrodos:} Son pequeños sensores colocados en el cuero cabelludo según el sistema internacional 10-20. Estos electrodos miden los cambios de voltaje producidos por la actividad eléctrica de las neuronas. Cada electrodo detecta la actividad en una región específica del cerebro, permitiendo un mapeo detallado de su actividad.
    \item \textbf{Amplificador:} Las señales eléctricas generadas por el cerebro son muy débiles, típicamente entre 0.5 a 100 μV. El amplificador del EEG aumenta estas señales, permitiendo que puedan ser procesadas y visualizadas. En algunos dispositivos avanzados, se utilizan técnicas de amplificación diferencial para mejorar la relación señal-ruido.
    \item \textbf{Conversor analógico-digital:} Las señales eléctricas captadas son analógicas, por lo que se requiere un conversor analógico-digital para traducirlas a un formato digital que pueda ser procesado por computadoras. La resolución del ADC es crítica, ya que define la precisión con la que las señales son capturadas.
    \item \textbf{Software de procesamiento:} El software realiza el filtrado y procesamiento de las señales crudas para eliminar el ruido o artefactos no relacionados con la actividad cerebral, como los generados por movimientos o interferencias eléctricas. Además, permite el análisis en tiempo real de las ondas cerebrales (Delta, Theta, Alpha, Beta, Gamma) y su interpretación para diversas aplicaciones, como estudios clínicos o interfaces cerebro-computadora.
    \item \textbf{Pantalla/Gráficos:}El electroencefalógrafo muestra las señales eléctricas como gráficos de ondas cerebrales. Estas ondas reflejan diferentes estados mentales, como relajación, concentración o sueño, y son analizadas por especialistas para determinar la actividad neurológica o la respuesta ante estímulos específicos.
\end{itemize}

\subsubsection{Aplicaciones del EEG}
\begin{itemize}
    \item \textbf{Diagnóstico clínico:} Es utilizado para diagnosticar y monitorear trastornos neurológicos como la epilepsia, trastornos del sueño, y diversas encefalopatías.
    \item \textbf{Investigación neurocientífica:} Permite estudiar los mecanismos del cerebro, la plasticidad cerebral, y las respuestas neuronales ante diversos estímulos.
    \item \textbf{Interfaces cerebro-computadora (BCI):} Las señales EEG pueden ser procesadas para controlar dispositivos, como sillas de ruedas eléctricas o prótesis, mediante la detección de patrones específicos de actividad cerebral.
    \item \textbf{Monitoreo intraoperatorio:} Durante cirugías neurológicas, el EEG puede utilizarse para monitorear la actividad cerebral en tiempo real y evitar daños en áreas críticas del cerebro.
\end{itemize}

\subsection{Cantidad de canales}
En el diseño de nuestra silla de ruedas controlada mediante señales cerebrales, hemos optado por un sistema de 4 canales con 9 electrodos (4 positivos, 4 negativos y 1 de masa) por varias razones clave, que refuerzan la precisión, la confiabilidad y la calidad de la señal capturada.

\begin{enumerate}
    \item \textbf{Optimización de la Captura de Señales EEG} 
    
    El cerebro humano emite diferentes tipos de ondas cerebrales (alfa, beta, gamma, delta y theta) que se distribuyen de manera no uniforme a lo largo del cuero cabelludo. Al utilizar 4 canales con 4 pares de electrodos (positivos y negativos) podemos capturar señales de distintas áreas cerebrales simultáneamente. Esto nos permite recoger información más completa y representativa de la actividad cerebral relevante para el control de la silla de ruedas.
    \item \textbf{Mayor Resolución en la Separación de Patrones Cerebrales} 
    
    El uso de múltiples electrodos garantiza una mayor resolución espacial en la detección de ondas cerebrales. Al disponer de 4 canales, podemos asociar cada canal a diferentes áreas de interés cerebral (como las regiones motoras o visuales), lo que aumenta la capacidad del sistema de IA para interpretar correctamente los patrones de ondas que se correlacionan con las intenciones de movimiento. Esto es crítico en una interfaz cerebro-computadora (BCI), donde la precisión es esencial para evitar errores en la dirección del movimiento.
    \item \textbf{Minimización de Ruido y Artefactos} 
    
    Cada par de electrodos está configurado en un modo diferencial, lo que nos ayuda a minimizar el ruido de fondo y los artefactos externos, como el ruido eléctrico del entorno o movimientos involuntarios. Los 4 electrodos negativos actúan como referencias de los positivos, de modo que la diferencia de potencial entre ellos permite eliminar parte del ruido que pudiera interferir en la calidad de la señal. Esto mejora considerablemente la relación señal/ruido y asegura una detección más precisa de las señales relevantes.
    \item \textbf{Uso del Electrodo de Masa para Estabilizar las Mediciones }
    
    El electrodo de masa se utiliza para estabilizar el sistema y reducir el ruido eléctrico residual. Este electrodo está conectado a un punto de referencia neutro, lo que permite estabilizar los potenciales medidos en los otros electrodos, asegurando que las fluctuaciones o interferencias no alteren la calidad de las señales EEG. La masa es esencial para la precisión global del sistema, evitando desequilibrios de voltaje que podrían provocar lecturas erróneas.
    \item \textbf{Equilibrio entre Complejidad y Procesamiento:}
    
    Optamos por 4 canales ya que representan un equilibrio adecuado entre complejidad técnica y capacidad de procesamiento. Más canales implicarían una mayor carga computacional para la Raspberry Pi 4, lo que podría requerir un hardware más potente o provocar retrasos en el procesamiento de las señales en tiempo real. Con esta configuración, logramos un sistema eficiente y suficiente para captar las señales necesarias sin comprometer la velocidad de respuesta del sistema de control de la silla.
    \item \textbf{Compatibilidad con el 'Sistema 10-20'} 
    
    La disposición de los electrodos sigue el estándar del 'Sistema 10-20' para garantizar una colocación uniforme y científicamente validada en el cuero cabelludo. Esto nos permite seleccionar puntos específicos que optimicen la captación de señales relevantes para nuestro sistema BCI, alineándonos con prácticas clínicas y de investigación que han demostrado ser efectivas en la medición de la actividad cerebral.
\end{enumerate}

El uso de estos filtros permite separar de manera efectiva las señales cerebrales del ruido presente en el entorno. Esto garantiza que las señales capturadas sean lo suficientemente limpias y precisas para su procesamiento por la Raspberry Pi 4. El diseño del sistema de filtrado incluye tanto filtros de paso bajo como de paso alto, optimizados para cada banda de frecuencia, lo que mejora la fiabilidad del control basado en las ondas cerebrales.

\subsection{Sistema 10-20}

El sistema 10-20 es un método internacionalmente estandarizado para la colocación de electrodos en el cuero cabelludo durante un electroencefalograma (EEG). Este sistema asegura que los electrodos se coloquen de manera uniforme y precisa en relación con los puntos anatómicos del cráneo, permitiendo una medición consistente y reproducible de la actividad eléctrica cerebral.

El nombre "10-20" proviene de las distancias porcentuales entre los electrodos: Los electrodos se colocan en posiciones que están al 10\% o al 20\% de la distancia total entre puntos anatómicos clave del cráneo.
Puntos anatómicos clave de referencia:
\begin{itemize}
    \item \textbf{Nasion:} El punto entre la frente y la nariz.
    \item \textbf{Inion:} El punto más prominente en la parte posterior de la cabeza.
    \item \textbf{Puntos preauriculares:} Justo por encima de los oídos, a cada lado de la cabeza.
\end{itemize}

Las posiciones de los electrodos se distribuyen sobre la cabeza tomando como referencia estos puntos para cubrir todo el cuero cabelludo de forma equidistante.

\begin{figure}[H]
    \centering
    
    \caption{Puntos de medicion de Ondas Cerebrales}
    \label{fig:enter-label}
\end{figure}

\subsubsection{¿Para qué sirve?}
El sistema 10-20 se utiliza para garantizar una colocación precisa y consistente de los electrodos en los estudios de EEG. Algunos de sus beneficios incluyen:

\begin{itemize}

    \item \textbf{Estandarización global:} Permite que los estudios de EEG sean comparables en diferentes laboratorios y entre diferentes pacientes.
    \item \textbf{Cobertura completa del cerebro:} El sistema asegura que se cubran adecuadamente diferentes áreas del cerebro (frontal, parietal, occipital, temporal).
    \item \textbf{Detección de anomalías:} Facilita la identificación de regiones del cerebro donde pueden estar ocurriendo fenómenos anormales, como descargas epilépticas, actividad lenta anormal o asimetrías en las ondas cerebrales.
    
\end{itemize}

\subsubsection{¿Como se aplica?}

En un estudio de EEG, se colocan electrodos en el cuero cabelludo siguiendo estas posiciones predeterminadas en el sistema 10-20:

\begin{enumerate}
    \item Puntos y nomenclatura: Cada posición de electrodo tiene una nomenclatura que se utiliza para identificar las regiones del cerebro de las que se está registrando la actividad.
\end{enumerate}

\begin{itemize}
    \item F: Frontal (F3, F4, Fz, etc.)
    \item C: Central (C3, C4, Cz, etc.)
    \item P: Parietal (P3, P4, Pz, etc.)
    \item O: Occipital (O1, O2)
    \item T: Temporal (T3, T4, etc.)
    \item Los números impares (1, 3, 5, 7) se asignan al hemisferio izquierdo, mientras que los números pares (2, 4, 6, 8) se asignan al hemisferio derecho. La letra "z" indica posiciones centrales (a lo largo de la línea media de la cabeza).
\end{itemize}

\subsubsection{Pasos para aplicar el sistema 10-20}

\begin{enumerate}

    \item \textbf{Medición del cráneo:} Se mide la distancia desde el nasion al inion y desde un punto preauricular al otro. Luego, se calculan los puntos intermedios en un 10 o 20 de esas distancias para determinar las ubicaciones exactas de los electrodos.
    
    \item \textbf{Colocación de los electrodos:} Se colocan electrodos en los puntos marcados, asegurando una cobertura uniforme de la cabeza. Esto puede hacerse usando una gorra de EEG con posiciones ya marcadas o mediante la medición manual.
    
    \item \textbf{Registro de la actividad:} Una vez colocados los electrodos, se inicia el registro de la actividad cerebral. Los electrodos miden las diferencias de potencial eléctrico entre las regiones del cerebro cubiertas por los electrodos.
\end{enumerate}

\subsubsection{Aplicaciones del sistema 10-20}
\begin{itemize}
    \item \textbf{Diagnóstico clínico:} El sistema se usa comúnmente en estudios de EEG para diagnosticar condiciones neurológicas como la epilepsia, trastornos del sueño, y daño cerebral.
    \item \textbf{Investigación:} En estudios de neurociencia, el sistema 10-20 facilita la comparación de la actividad cerebral entre sujetos, ya que la ubicación de los electrodos está estandarizada.
    \item \textbf{Interfaces cerebro-computadora (BCI):} En proyectos de BCI, se utiliza el sistema 10-20 para colocar electrodos en áreas específicas del cerebro que controlan movimientos o funciones específicas.
\end{itemize}

\subsubsection{Colocacion de Electrodos}
Para llevar a cabo el registro de las señales EEG, es necesario disponer adecuadamente los electrodos. En nuestro proyecto, utilizamos un total de 9 electrodos, distribuidos en 4 canales: 4 electrodos positivos, 4 negativos y 1 de masa.

Los puntos de medición seleccionados para la colocación de los electrodos son los siguientes: Fp1, Fp2, F7, F8, T3, T4, O1, O2 y A2. Es importante señalar que los electrodos positivos se colocan en el lado derecho del cuero cabelludo (Fp2, F8, T4 y O2), mientras que los electrodos negativos se ubican en el lado izquierdo (Fp1, F7, T3 y O1). El electrodo de referencia o masa se posiciona en el lóbulo de la oreja, en el punto A2.

\subsection{Raspberry Pi 4}
La Raspberry Pi 4 es una computadora de bajo costo y tamaño compacto que se utiliza en una gran variedad de aplicaciones, especialmente en proyectos de electrónica, IoT (Internet of Things), y sistemas embebidos. Fue desarrollada por la Fundación Raspberry Pi para fomentar la educación en ciencias de la computación y se ha popularizado en proyectos de prototipado debido a su flexibilidad, potencia, y precio accesible.

\begin{figure}[H]
    \centering
    
    \caption{Raspberry Pi 4 PinOut}
    \label{fig:enter-label}
\end{figure}

\subsubsection{Caracteristicas de la RPi4}
\begin{itemize}
    \item \textbf{Procesador:} Broadcom BCM2711, quad-core Cortex-A72 (ARM v8) de 64 bits a 1.5GHz.
    \item \textbf{Memoria RAM:} Existen variantes con 2GB, 4GB y 8GB de RAM LPDDR4.
    \item \textbf{Puertos USB:} 2 puertos USB 3.0 y 2 puertos USB 2.0.
    \item \textbf{Conectividad:} Ethernet Gigabit, WiFi 802.11ac, Bluetooth 5.0.
    \item \textbf{Salidas de video:} Dos puertos micro-HDMI, capaces de soportar resoluciones 4K.
    \item \textbf{Almacenamiento:} No tiene disco duro interno, pero se utiliza una tarjeta microSD para almacenar el sistema operativo y los archivos.
    \item \textbf{Puertos GPIO:} 40 pines GPIO (General Purpose Input/Output) para conectar diversos componentes electrónicos, como sensores, actuadores y módulos de comunicación.
    \item \textbf{Alimentación:} Requiere una fuente de alimentación de 5V/3A mediante un puerto USB-C.
\end{itemize}

\subsubsection{Uso de la Raspberry Pi 4 en la silla}
Los pines GPIO de la Raspberry Pi 4 permiten interactuar con una variedad de componentes, como sensores, actuadores y módulos de comunicación. En nuestro proyecto, utilizamos estos pines para:

\begin{itemize}
    \item \textbf{Control de Motores:} A través de los pines GPIO, enviamos señales a los controladores de motores que ajustan la velocidad y dirección de los mismos, permitiendo los movimientos precisos de la silla de ruedas.
    \item \textbf{Recepción de Señales EEG:} Las señales EEG provenientes de los electrodos colocados en el cuero cabelludo se procesan con un convertidor ADC (convertidor de señal análoga a digital) y se envían a la Raspberry Pi para su análisis y clasificación en tiempo real.
    \item \textbf{Sistema de Emergencia:} La Raspberry Pi se encarga de controlar los sensores ultrasónicos ubicados en diferentes puntos de la silla de ruedas, activando LEDs y un buzzer cuando se detectan obstáculos en la trayectoria.
\end{itemize}

\subsubsection{Programacion con la RPi4}
La programación de la Raspberry Pi 4 se realiza principalmente en Python debido a su versatilidad y al soporte de bibliotecas específicas, como gpiozero, que facilita el control de los pines GPIO. En nuestro proyecto, Python se utiliza para las siguientes funciones:
\begin{itemize}
    \item \textbf{Procesamiento de Señales EEG:} Implementamos algoritmos que procesan las señales EEG en tiempo real utilizando filtros digitales y técnicas de análisis, como CAR (Common Average Reference) y ICA (Independent Component Analysis), para identificar los comandos que controlan la dirección de la silla.
    \item \textbf{Control de Motores y Sensores:} Se desarrolla un programa para controlar los motores y gestionar el sistema de emergencia, combinando datos de los sensores ultrasónicos con los comandos derivados de las señales EEG.
\end{itemize}
Gracias a su procesador de cuatro núcleos y opciones de memoria de hasta 8 GB, la Raspberry Pi 4 puede ejecutar múltiples tareas simultáneamente. Esto permite que el sistema realice el procesamiento de señales EEG, el control de motores y la gestión del sistema de emergencia sin interrupciones. Para maximizar la eficiencia, se han implementado técnicas de multithreading en el código, lo que permite que diferentes procesos se ejecuten en paralelo.

\subsubsection{Aplicaciones Generales de la RPi4}
Además de su uso en nuestro proyecto de silla de ruedas, la Raspberry Pi 4 tiene múltiples aplicaciones, entre las que se destacan:

\begin{itemize}
    \item \textbf{Automatización y Robótica:} Control de sistemas de robótica, como vehículos autónomos o robots, con la capacidad de gestionar múltiples sensores y motores simultáneamente.
    \item \textbf{Centros de Medios:} Configuración de servidores multimedia utilizando herramientas como Kodi, para la reproducción de videos y música.
    \item \textbf{IoT (Internet of Things):} Monitorización y control de dispositivos conectados a internet, como sistemas de seguridad, domótica y más.
    \item \textbf{Estaciones de Monitoreo:} Implementación de estaciones meteorológicas o de monitorización ambiental utilizando sensores conectados a los pines GPIO.
    \item \textbf{Proyectos Educativos:} Gracias a su bajo costo y la abundancia de recursos educativos, la Raspberry Pi es ideal para enseñar conceptos de programación, electrónica y robótica.
\end{itemize}

\subsection{Comunicación UART}

El UART (Universal Asynchronous Receiver-Transmitter) es un periférico de hardware utilizado para la comunicación serie. Su principal función es permitir la transmisión y recepción de datos de manera asíncrona, lo que implica que no requiere de una señal de clock compartida entre el transmisor y el receptor. A continuación, se destacan las características principales de este tipo de comunicación:

\begin{itemize}
    \item \textbf{Comunicación serie:} Los datos se transmiten de forma secuencial, bit a bit, a través de una línea de transmisión (TX) y se reciben mediante una línea de recepción (RX).
    \item \textbf{Asincronía:} Al no utilizar una señal de clock constante, ambos dispositivos deben estar configurados con la misma velocidad de transmisión (tasa de baudios) para asegurar la correcta recepción de los datos.
    \item \textbf{Formato de datos:} Cada paquete de datos transmitido generalmente incluye un bit de inicio (indicando el comienzo de la transmisión), entre 5 y 9 bits de datos, un bit opcional de paridad (para detección de errores), y uno o dos bits de parada.
    \item \textbf{Velocidad de transmisión:} La velocidad de transmisión de la información, conocida como tasa de baudios, se refiere al número de bits transmitidos por segundo.
\end{itemize}

La implementación de la comunicación UART en nuestro proyecto se utiliza para la recepción y procesamiento de señales. Específicamente, en la RP2040 Zero, enviamos las lecturas de los cuatro canales del ADC (Conversor Analógico-Digital) en formato JSON durante un período de tiempo definido y con una frecuencia de muestreo específica a la Raspberry Pi 4.

\begin{figure}[H]
    \centering
    
    \caption{Comuniacion UART}
    \label{fig:enter-label}
\end{figure}

\begin{figure}[H]
    \centering
    
    \caption{Envio de datos de UART}
    \label{fig:enter-label}
\end{figure}

\subsection{Gráfico de Fourier}
El gráfico de Fourier está basado en la Transformada de Fourier (TF), que es una operación matemática que descompone una señal en sus componentes sinusoidales de diferentes frecuencias. Este método es especialmente útil para analizar señales periódicas y no periódicas.

La Transformada de Fourier dicta que: 

Dada una señal \textit{x(t)} en el dominio del tiempo, la transformada de Fourier \textit{X(f)} se define como:

\begin{figure}[H]
    \centering
    
\end{figure}

\newpage
Donde:
\begin{itemize}
    \item \textit{x(t)} es la señal en el dominio del tiempo.
    \item \textit{X(f)} es la señal transformada en el dominio de la frecuencia.
    \item \textit{f} es la frecuencia (Hz).
    \item \textit{j} es la unidad imaginaria 
    \item $e^{-j2\pi ft}$ es la función compleja que representa la descomposición en sinusoides.

\end{itemize}

El gráfico de Fourier representa la magnitud o la fase de la transformada de Fourier. Este gráfico tiene dos componentes importantes:

\begin{enumerate}
    \item \textbf{Espectro de Magnitud:} Se representa gráficamente la magnitud de cada frecuencia presente en la señal. En el eje horizontal está la frecuencia \textit{f}, y en el eje vertical está la magnitud |\textit{X(f)}|, que indica cuánta energía o potencia de la señal está concentrada en esa frecuencia específica.

    \begin{equation}
        |X(f)| = \sqrt{Re(X(f))^2+Im(X(f))^2}
    \end{equation}
    
    \item \textbf{Espectro de Fase:} Indica el desfase de cada frecuencia con respecto a la señal original. En el eje horizontal también está la frecuencia \textit{f}, y en el eje vertical está el ángulo de fase \theta(f), $ que puede calcularse como:

    \begin{equation}
        \theta = tan^{-1} \left(\frac{Im(X(f))}{a}\right)
        \label{eq:1}
    \end{equation}
\end{enumerate}

\begin{figure}[H]
    \centering
    
    \caption{Grafico de Fourier}
    \label{fig:enter-label}
\end{figure}

\subsubsection{¿Para que sirve?}
El grafico de Fourier es una herramienta que sirve para analizar señales en el dominio de la frecuencia.
\newpage
\begin{enumerate}
    \item \textbf{Análisis de frecuencias:}
    \begin{itemize}
        \item \textbf{Descomposición de señales complejas:} Permite descomponer una señal en sus componentes de frecuencia individuales. Esto es útil cuando quieres saber qué frecuencias están presentes en una señal y su importancia relativa.
    
        \item \textbf{Identificación de frecuencias dominantes:} El gráfico te muestra cuáles son las frecuencias que más contribuyen a la señal original, lo que es esencial para entender fenómenos periódicos y patrones.
    \end{itemize}
    \item \textbf{Filtrado de señales:}
    \begin{itemize}
        \item \textbf{Diseño de filtros:} Si necesitas eliminar ruido o componentes no deseados de una señal, el gráfico de Fourier ayuda a identificar las frecuencias del ruido o interferencia. Luego puedes diseñar un filtro que elimine esas frecuencias.
    
        \item \textbf{Filtrado de bandas:} Puedes aplicar filtros pasa-bajas, pasa-altas o de banda (pasa-banda o elimina-banda) a una señal. El gráfico te muestra exactamente qué frecuencias están siendo afectadas.
    \end{itemize}
    
    \item \textbf{Compresión de datos:}
    \begin{itemize}
        \item \textbf{ Eliminación de información redundante:} En algunas señales (como imágenes o audio), las frecuencias más altas o muy bajas pueden no ser necesarias. Usando el gráfico de Fourier, puedes identificar esas frecuencias y eliminarlas para comprimir los datos sin perder información relevante.
    
        \item \textbf{Compresión de audio e imágenes:} Muchos algoritmos de compresión (como JPEG o MP3) utilizan la Transformada de Fourier o versiones discretas de ella para eliminar componentes de alta frecuencia que son menos perceptibles para el ser humano.
    \end{itemize}
    
    \item \textbf{Análisis de vibraciones y ondas:}
    \begin{itemize}
        \item \textbf{Detección de fallos en maquinaria:} En ingeniería mecánica y de control, el gráfico de Fourier es utilizado para analizar vibraciones y detectar problemas como desbalances, resonancias, o desgastes en partes móviles. Las frecuencias anómalas pueden señalar fallos.
    
        \item \textbf{Análisis de señales acústicas:} Permite estudiar el espectro de frecuencias en señales de audio. Por ejemplo, para identificar las características de sonidos musicales o voces.
    \end {itemize}
    
    \item \textbf{Procesamiento de señales EEG:}
    \begin{itemize}
        \item Para el análisis de señales cerebrales (EEG), el gráfico de Fourier es vital para identificar y separar las diferentes bandas de frecuencias asociadas con diferentes actividades cerebrales (como las ondas delta, theta, alpha, beta y gamma).
    
        \item \textbf{Monitoreo de actividad cerebral:} En neurociencia, el análisis de Fourier se utiliza para analizar patrones de actividad cerebral, detectar anormalidades y realizar interfaces cerebro-máquina (como el control de la silla de ruedas en tu proyecto).
    \end{itemize}
    \item \textbf{Análisis de señales en telecomunicaciones:}
    \begin{itemize}
        \item \textbf{Ancho de banda:} El gráfico de Fourier permite determinar el ancho de banda necesario para transmitir una señal sin pérdida de información.
    
        \item \textbf{Modulación y demodulación:} En sistemas de comunicaciones, la modulación de señales se realiza en el dominio de la frecuencia. El gráfico de Fourier te permite visualizar cómo una señal ha sido modulada para su transmisión y cómo se puede demodular para su interpretación.
    \end{itemize}
    \newpage
    \item \textbf{Análisis de imágenes:}
    \begin{itemize}
        \item \textbf{Reconocimiento de patrones:} En procesamiento de imágenes, la transformada de Fourier se utiliza para identificar patrones repetitivos o estructuras de frecuencia en una imagen. Es útil en tareas como la detección de bordes o compresión de imágenes.
    
        \item \textbf{Eliminación de ruido:} Permite eliminar patrones específicos de ruido en imágenes filtrando frecuencias indeseadas.
    \end{itemize}
\end{enumerate}

\subsubsection{¿En que lo aplicamos?}

Se emplea el Análisis de Fourier para identificar el espectro de frecuencias de las señales cerebrales, permitiendo la diferenciación de las ondas alpha, beta, gamma, delta y theta. Posteriormente, se aplica la Transformada Inversa de Fourier para reconstruir las señales en el dominio temporal, recuperando su forma original.

Una vez que las señales han sido diferenciadas por bandas de frecuencia, el algoritmo de machine learning procede a extraer las características (features) de cada tipo de onda a partir de una representación en el dominio de la frecuencia y del tiempo. Estas características son utilizadas para realizar la predicción del movimiento deseado en la silla de ruedas.

\subsubsection{¿Que es una feature?}

Una feature es una propiedad medible o una característica distintiva de un fenómeno. En el contexto de este proyecto, las features se refieren a las propiedades específicas de cada señal cerebral, clasificadas por tipo de onda (alpha, beta, gamma, delta y theta). Estas propiedades son extraídas para capturar la información relevante que permitirá al sistema de aprendizaje automático identificar patrones en las señales y realizar predicciones relacionadas con el control de la silla de ruedas.

\subsection{Filtros digitales}

Un filtro digital es una herramienta utilizada en el procesamiento de señales para modificar o mejorar ciertos aspectos de una señal digital, eliminando o atenuando componentes no deseados, como ruido, o destacando componentes útiles. Los filtros digitales operan sobre señales discretizadas (muestreadas) y utilizan algoritmos matemáticos para realizar diversas transformaciones.

Existen diferentes tipos de filtros digitales, según su función:

\begin{itemize}
    \item \textbf{Filtro pasa bajas:} Permite el paso de frecuencias bajas y atenúa las frecuencias altas.
    \item \textbf{Filtro pasa altas:} Permite el paso de frecuencias altas y atenúa las bajas.
    \item \textbf{Filtro pasa banda:} Permite el paso de un rango específico de frecuencias.
    \item \textbf{Filtro elimina banda (Notch):} Atenúa un rango específico de frecuencias, como en el caso de eliminar interferencias a 50-60 Hz.
\end{itemize}

Los filtros digitales pueden ser FIR (Finite Impulse Response) o IIR (Infinite Impulse Response):

\begin{itemize}
    \item Los filtros FIR tienen una respuesta finita y son más estables, pero pueden necesitar más recursos de procesamiento.
    \item Los filtros IIR tienen una respuesta infinita y suelen ser más eficientes en términos de recursos, pero pueden ser menos estables si no se diseñan correctamente.
\end{itemize}

Los filtros digitales son ampliamente usados en aplicaciones como procesamiento de audio, señales biológicas (como EEG), imágenes y telecomunicaciones.
\subsubsection{¿Para que los necesitamos si ya tenemos por Hardware?}
La combinación de filtros físicos (implementados en hardware) con filtros digitales (implementados en software) presenta una serie de ventajas significativas, incluso si ya se han instalado filtros físicos en el sistema. Aunque los filtros basados en hardware permiten un filtrado efectivo de las señales EEG, los filtros digitales proporcionan una flexibilidad y capacidades adicionales que no siempre son posibles de lograr mediante hardware exclusivamente. A continuación, se detallan las razones por las cuales puede ser beneficioso incorporar filtros digitales a la salida de los filtros físicos:
\begin{enumerate}
    \item \textbf{Ajuste Preciso y Mayor Flexibilidad}
    
    Los filtros de hardware están limitados a sus parámetros iniciales, ya que una vez construidos con componentes específicos (como resistencias, condensadores, etc.), sus características clave, tales como la frecuencia de corte y el ancho de banda, son difíciles de modificar. En contraste, los filtros digitales permiten ajustar fácilmente parámetros como la frecuencia de corte o la configuración de filtrado sin necesidad de realizar cambios físicos. Esto resulta especialmente útil cuando, tras el análisis de la señal, es necesario ajustar el rango de paso de un filtro o eliminar una frecuencia no contemplada inicialmente. Además, los filtros digitales permiten realizar modificaciones rápidas y sin intervención física, optimizando la eficiencia del proceso.
    \item \textbf{Compensación de las Limitaciones Intrínsecas del Hardware}
    
    Los filtros físicos, aunque efectivos, no son perfectos. Su desempeño puede verse afectado por tolerancias en los componentes o por factores ambientales, como la temperatura y el envejecimiento de los mismos. Los filtros digitales, por su parte, pueden corregir o complementar las imperfecciones de los filtros de hardware. Por ejemplo, si un filtro físico no consigue eliminar completamente el ruido de 50 Hz o presenta desviaciones mínimas en las frecuencias de corte, un filtro digital puede ajustarse con precisión para corregir estas deficiencias, mejorando así la calidad general del filtrado.
    \item \textbf{Filtrado Adaptativo en Tiempo Real}
    
    Los filtros físicos son estáticos, lo que significa que su comportamiento es constante y no varía según las condiciones de la señal. En cambio, un filtro digital ofrece la posibilidad de implementar técnicas de filtrado adaptativo, es decir, que el filtro ajuste sus características en función de las condiciones cambiantes de la señal. Esto es especialmente beneficioso en entornos donde las condiciones son variables, como cuando la interferencia de 50 Hz no está presente de manera constante. Un filtro digital adaptativo puede activarse solo cuando detecta interferencias, optimizando el procesamiento de la señal en tiempo real. De esta manera, el sistema EEG se ajusta de manera dinámica, lo que puede incrementar la fiabilidad del procesamiento.
    \item \textbf{Procesamiento Avanzado y Filtrado de Alta Precisión}
    
    La complejidad de los filtros físicos está limitada por los componentes que los conforman. Sin embargo, en el ámbito digital es posible implementar filtros de mayor complejidad y orden, permitiendo un filtrado más preciso y específico. Los filtros digitales de mayor orden ofrecen transiciones más nítidas entre las bandas de paso y de rechazo. Por ejemplo, con un filtro digital, es posible eliminar una banda estrecha de ruido sin afectar las frecuencias adyacentes de interés, algo difícil de lograr mediante componentes físicos convencionales.
    \item \textbf{Filtrado en Múltiples Etapas}
    
    El uso de filtrado digital permite procesar la señal en diferentes etapas, lo que resulta en un análisis más profundo y detallado de las señales EEG. Tras el paso por los filtros físicos, se pueden aplicar diferentes tipos de filtros digitales para aislar aspectos específicos de la señal que no fueron manejados por el filtrado físico. Por ejemplo, se pueden implementar filtros pasa banda específicos para resaltar ciertas bandas de ondas cerebrales, como las ondas alpha o beta, o utilizar técnicas avanzadas como el Análisis de Componentes Independientes (ICA) para separar señales superpuestas o interferencias no deseadas. El uso de filtros adaptativos también permite ajustar continuamente la respuesta del sistema, optimizando el rendimiento del procesamiento de señales.
    \item \textbf{Posprocesamiento y Análisis Selectivo}
    
    El filtrado digital permite realizar un análisis detallado de las señales EEG en una etapa posterior, ya sea sobre los datos almacenados o sobre la señal adquirida en tiempo real. Este posprocesamiento es fundamental para detectar patrones específicos o eliminar artefactos que no fueron suficientemente atenuados en la etapa inicial de filtrado físico. Por ejemplo, los artefactos relacionados con el movimiento o las señales de baja frecuencia, como la respiración, pueden requerir un ajuste adicional después de la adquisición de la señal. Además, un análisis más exhaustivo en tiempo real puede detectar elementos que los filtros de hardware no lograron capturar completamente.
    \item \textbf{Redundancia y Seguridad}
    
    Incorporar tanto filtros físicos como digitales en un sistema de procesamiento de señales EEG añade una capa extra de seguridad. Si un filtro físico falla o no cumple completamente su función, el filtro digital actúa como un sistema de respaldo, asegurando que el ruido y las interferencias no afecten el análisis de la señal. Esta redundancia es clave en entornos críticos donde se necesita garantizar la integridad y pureza de los datos EEG para obtener resultados confiables y precisos.
\end{enumerate}

\subsection{Gel conductor}
El gel conductor neutro empleado en los electroencefalogramas (EEG) es una sustancia formulada para optimizar la conductividad eléctrica entre los electrodos y el cuero cabelludo del paciente. Su principal objetivo es minimizar la resistencia entre los electrodos y la piel, garantizando una transmisión eficiente y sin interferencias de las señales eléctricas cerebrales hacia los electrodos. 

\subsubsection{Cómo aplicar el gel conductor}
En los electrodos de copa dorada, el procedimiento consiste únicamente en rellenar la cavidad de la copa con el gel conductor, posteriormente colocarlo sobre una zona del cuero cabelludo previamente limpiada con algodón, mantenerlo en posición durante unos segundos y eliminar cualquier exceso de gel, en caso de haberlo, con un pequeño trozo de papel. Utilizamos este gel en el proyecto con el fin de obtener la mejor calidad posible en las señales, además de generar un leve efecto de succión que contribuye a mantener los electrodos firmemente adheridos.

\subsection{Jaula de Faraday}
Una Jaula de Faraday es una estructura cerrada o parcialmente cerrada hecha de un material conductor (como metal), diseñada para bloquear campos electromagnéticos externos. El principio detrás de la jaula de Faraday fue descubierto por el físico Michael Faraday en 1836, quien observó que una caja hecha de material conductor podía proteger su interior de influencias electromagnéticas.

Cuando un campo electromagnético externo impacta en la superficie de la jaula, las cargas eléctricas libres en el material conductor se redistribuyen, anulando el campo dentro de la estructura. Como resultado, cualquier dispositivo o sistema ubicado dentro de la jaula está protegido de la interferencia electromagnética (EMI) o de campos eléctricos externos.

\subsubsection{Principio de Funcionamiento}
El funcionamiento de la jaula de Faraday se basa en la redistribución de cargas eléctricas. Cuando una onda electromagnética incide sobre la superficie de la jaula las cargas en el material conductor de la jaula se reacomodan, generando un campo eléctrico que contrarresta el campo incidente. Este campo interno es tal que cancela el campo electromagnético externo dentro de la jaula. Como consecuencia, el campo eléctrico dentro de la jaula es nulo, protegiendo su interior de interferencias externas.

Es importante mencionar que, aunque la jaula de Faraday bloquea la mayoría de las frecuencias electromagnéticas, la eficacia del bloqueo depende del tamaño de las aperturas en la jaula y la frecuencia de la señal. Cuanto más pequeña sea la apertura respecto a la longitud de onda de la señal externa, mayor será la efectividad de la protección.

\subsubsection{¿Para que sirve?}
El propósito principal de una jaula de Faraday es proteger su contenido contra interferencias electromagnéticas (EMI) y campos eléctricos indeseados. Esto es particularmente importante en ambientes donde la estabilidad de las señales eléctricas o electromagnéticas es crucial. Algunas de sus aplicaciones comunes incluyen:
\begin{itemize}
    \item \textbf{Protección de Dispositivos Electrónicos:} Los dispositivos sensibles pueden verse afectados por interferencias electromagnéticas que podrían alterar su funcionamiento. La jaula de Faraday protege estos dispositivos, asegurando su funcionamiento adecuado.
    \item \textbf{Experimentos Científicos:} En laboratorios, se utilizan jaulas de Faraday para eliminar interferencias en experimentos sensibles a campos eléctricos o electromagnéticos.
    \item \textbf{Sistemas de Comunicaciones:} Para evitar que las señales de radiofrecuencia interfieran en comunicaciones o dispositivos electrónicos, se emplean jaulas de Faraday en recintos y cámaras anecoicas.
    \item \textbf{Protección Contra Ataques Electromagnéticos (EMP):} En algunos casos, las jaulas de Faraday se emplean para proteger equipos contra pulsos electromagnéticos generados de manera natural (por tormentas solares) o artificial (por explosiones nucleares o dispositivos EMP).
\end{itemize}

\subsubsection{Como se utiliza}
El diseño y construcción de una jaula de Faraday varía dependiendo del propósito específico, pero los principios generales de uso son los siguientes:
\begin{itemize}
    \item \textbf{Materiales Conductores:} La jaula debe estar hecha de un material conductor, generalmente aluminio, cobre o acero. Cuanto mejor sea el conductor, más efectiva será la jaula para bloquear campos electromagnéticos.
    \item \textbf{Aperturas Pequeñas:} Si la jaula tiene ventanas o aperturas, estas deben ser pequeñas en comparación con la longitud de onda de las señales que se desea bloquear. Por ejemplo, las mallas metálicas con agujeros finos son efectivas para bloquear frecuencias de radio.
    \item \textbf{Aislamiento Completo:} Para garantizar que el campo electromagnético externo no penetre en el interior, la jaula debe estar cerrada por completo o con muy pequeñas aperturas.
    \item \textbf{Conexión a Tierra:} En algunos casos, se recomienda conectar la jaula a tierra para proporcionar un camino seguro para la disipación de cualquier carga acumulada.
\end{itemize}

\subsubsection{Aplicacion en la silla}
En nuestro proyecto, la jaula de Faraday juega un papel crucial para asegurar que las señales cerebrales recogidas por los electrodos EEG no sean afectadas por interferencias electromagnéticas externas. Las señales EEG son extremadamente débiles, y cualquier interferencia externa podría alterar su interpretación, lo que afectaría directamente el control de la silla. 

\newpage
Usamos la jaula de Faraday para:
\begin{itemize}
    \item \textbf{Protección de Señales EEG:} Las señales EEG tienen una amplitud muy baja, generalmente en el rango de microvoltios (µV), lo que las hace particularmente vulnerables a interferencias de otros dispositivos electrónicos o radiaciones electromagnéticas del ambiente (como WiFi, Bluetooth, teléfonos móviles, etc.). Sin protección, estas interferencias pueden introducir ruido en las señales, lo que dificultaría o impediría que los algoritmos de procesamiento interpreten correctamente las órdenes cerebrales para controlar el movimiento de la silla.
    \item \textbf{Estabilidad en el Procesamiento de Datos:} El uso de una jaula de Faraday en las proximidades del sistema de adquisición de señales EEG garantizará que las mediciones sean precisas y libres de ruidos, mejorando la eficiencia de los filtros y algoritmos utilizados para procesar las señales. Esto también permitirá que el sistema de IA reconozca patrones cerebrales con mayor fiabilidad.
    \item \textbf{Reducción de Interferencias Ambientales:} En entornos donde hay múltiples dispositivos electrónicos, como laboratorios, hospitales, o entornos industriales, las señales electromagnéticas pueden variar ampliamente. Al utilizar una jaula de Faraday, reducimos el impacto de estas fuentes de ruido externo en las señales EEG, lo que resulta en una mayor precisión en el control de la silla de ruedas.
    \item \textbf{Seguridad de los Datos:} Aunque no es una prioridad principal, la jaula de Faraday también puede actuar como un mecanismo de protección adicional para evitar que las señales de datos sean interceptadas o alteradas por fuentes externas maliciosas o no deseadas.
\end{itemize}

\subsubsection{Apantallamiento Electrico}
El apantallamiento eléctrico, también conocido como blindaje eléctrico, es un fenómeno que ocurre cuando un campo eléctrico externo es bloqueado o atenuado por un material conductor que lo rodea. Este principio se basa en la distribución de cargas eléctricas en un material conductor, que actúa como una barrera para evitar que el campo eléctrico externo afecte el espacio protegido.

El concepto de apantallamiento eléctrico está estrechamente relacionado con el funcionamiento de la jaula de Faraday. Cuando un conductor rodea un área en presencia de un campo eléctrico, las cargas en el conductor se redistribuyen de tal manera que cancelan el campo eléctrico dentro del área apantallada.

\subsection{¿Qué es un circuito de Offset?}

Un circuito de offset se utiliza para agregar un voltaje constante a una señal, desplazando su nivel de referencia sin cambiar la forma de la señal. Este tipo de circuito es común en sistemas de procesamiento de señales, donde se requiere ajustar el punto de referencia de una señal para que coincida con el rango de entrada de otro dispositivo o componente.

\textbf{Ejemplo de Funcionamiento}: Una señal de entrada, como una señal de corriente alterna (AC), puede presentar un rango de voltaje que oscila entre valores positivos y negativos, por ejemplo, una onda senoidal entre -5V y 5V.

Si se desea desplazar esta señal para que su rango esté comprendido entre 0V y 10V, se debe aplicar un voltaje de offset de 5V.

El circuito de offset sumará este valor constante de 5V a la señal, desplazando el rango completo de la misma hacia valores positivos, sin alterar su forma original.

\subsubsection{Utilización de Offsets}

En la sección de procesamiento y recepción, se implementó un circuito de offset para adaptar las señales, ya que la RP2040 Zero no es capaz de procesar señales con componentes negativos. Este ajuste permite una correcta recepción y, en consecuencia, un procesamiento completo de las señales. 

Las señales no irán más alla de los 9 Volts y -9 Volts, ya que este es el límite de la alimentación. La amplificación está calculada para que las señales normales cerebrales den un máximo de 3 Volts de amplitud. Por lo tanto, se utilizarán Zeners de 3,3 Volts en la entrada de la RP2040 Zero para evitar que le llegue una sobretensión a un pin de ADC. De esta forma, para cada pin de ADC se le inyecta un offset de 1,65 Volts para que, de esta forma, la lectura sea lo más grande y preciso posible.

\subsection{Sistema de emergencia}

La silla de ruedas está equipada con un sistema de emergencia basado en tecnología de ultrasonido, que se encuentra instalado en las direcciones principales del dispositivo. Este sistema tiene como propósito prevenir colisiones con objetos o cualquier tipo de obstáculo, protegiendo tanto al usuario como a la integridad de la silla. Cuando los sensores de ultrasonido detectan la presencia de un obstáculo cercano, se activa un indicador visual mediante un LED en la dirección del objeto, acompañado de una señal acústica generada por un buzzer. Simultáneamente, el sistema detiene el movimiento de la silla de ruedas de manera automática y procede a un tiempo de espera de unos segundos para evaluar si es seguro continuar el desplazamiento.

\subsection{Tipos de alimentaciones}

El proyecto opera con diferentes niveles de tensión de alimentación, siendo las principales fuentes de energía una batería de 24V y unas baterías recargables de 9V. La Raspberry Pi 4 requiere una alimentación de 5V, por lo cual se emplea un circuito regulador de tensión compuesto por un L7815 para reducir la tensión a 15V y, posteriormente, un L7805 para regularla a 5V.

El sistema de filtrado del EEG y la placa del sistema de Offset se alimentan mediante baterías recargables de 9V. En cuanto a la tarjeta RP2040 Zero, utilizada en el sistema Offset, esta recibe energía a través de un regulador de 5V derivado de las baterías de 9V. Los dispositivos del sistema de emergencia, como el buzzer y los sensores ultrasónicos, se alimentan a 5V a través de un pin de la Raspberry Pi 4 y del resto del sistema de control. Finalmente, los LED del sistema de emergencia son alimentados mediante los pines GPIO, los cuales proporcionan una salida de 3,3V.

\subsection{Sistema de control}

El sistema de control diseñado para este proyecto está compuesto por una Raspberry Pi 4, que tiene la responsabilidad de procesar las señales provenientes de los electrodos del electroencefalograma (EEG). A partir de este procesamiento, la Raspberry Pi 4 será capaz de interpretar las intenciones del usuario y, con base en ellas, determinar los movimientos correspondientes de la silla de ruedas. Este sistema se encuentra altamente integrado con la arquitectura de control, garantizando una respuesta precisa y fluida a las señales cerebrales del usuario.

Para la regulación del movimiento de los motores, se emplea modulación por ancho de pulso (PWM, por sus siglas en inglés), operando a una frecuencia de 50 Hz. La modulación por ancho de pulso es una técnica eficiente que permite controlar la velocidad y dirección de los motores mediante la variación del ciclo de trabajo. En este caso, cuando uno de los canales de PWM presenta un ciclo de trabajo del 25\%, mientras que el otro está en 0\%, se provoca el movimiento del motor en una dirección específica. Por otro lado, cuando ambos canales de PWM se encuentran en un ciclo de trabajo del 0\%, el motor permanece detenido, lo cual corresponde a una condición de reposo.

Es crucial tener en cuenta la existencia de un estado prohibido dentro de este esquema de control. Si ambos canales de PWM se configuran simultáneamente con un ciclo de trabajo del 25\%, se generaría una condición de cortocircuito, que podría dañar el sistema. El cortocircuito ocurre cuando las señales de los canales se anulan entre sí, generando una sobrecarga en los componentes, lo cual puede comprometer la integridad tanto de los motores como de los circuitos de control. Este escenario es considerado una condición crítica, y para evitar cualquier eventualidad peligrosa, se implementa un sistema de emergencias que actúa como una salvaguardia para el correcto funcionamiento del sistema.

El sistema de emergencias tiene la capacidad de detener el movimiento de los motores en el caso de que un obstáculo sea detectado en la dirección hacia la cual el usuario intenta moverse. Cuando se identifica tal situación, los motores se detienen inmediatamente, un buzzer emitirá un sonido de advertencia, y el LED correspondiente a la dirección obstruida se encenderá, proporcionando una señal visual clara de la situación. Este sistema no solo previene accidentes, sino que también mejora la seguridad del usuario al evitar colisiones involuntarias.

Cada una de las salidas del sistema, ya sea para la señalización PWM, los pines dedicados al buzzer, los sensores ultrasónicos o los LEDs, está directamente asociada a un GPIO (General-Purpose Input/Output) de la Raspberry Pi 4. Esta asociación permite un control preciso y eficiente de todos los componentes periféricos, asegurando que el sistema responda de manera coordinada y fiable a las señales de entrada y a las condiciones de emergencia detectadas.

\subsection{Puentes H}
Un Puente H es un circuito utilizado para invertir el sentido de giro de un motor y para separar su etapa de potencia con la de control. Su nombre viene de la forma gráfica que tiene el circuito. Se construye con 4 interruptores, pueden ser mecánicos o transistores. En la siguiente imágen se puede ver la forma de un puente H.

\begin{figure}[H]
    \centering
    
    \caption{Puente H Genérico por medio de llaves mecánicas}
\end{figure}

En este ejemplo, cuando la llave S1 y S4 se cierran, correrá corriente por esta rama, haciendo que el motor funcione y tenga un sentido de giro. Cuando la llave S2 y S3 se cierran, correrá corriente por esta rama también, pero con sentido de giro invertido. En este circuito, S1 y S2 nunca pueden estar cerradas al mismo tiempo, porque esto generaría un corto circuito, lo mismo con las llaves S3 y S4.

\begin{figure}[H]
    \centering
    
    \caption{Puente H Operando}
\end{figure}

\subsubsection{Puente H de potencia}
Un puente H de potencia es un tipo de circuito en el que la etapa de potencia, que incluye el motor, los transistores y está conectada a altas tensiones y corrientes, se encuentra separada de la etapa de control, la cual generalmente opera con voltajes más bajos. Esta separación se realiza para proteger la etapa de control de las altas tensiones, que podrían dañar o quemar sus circuitos. Podemos utilizar nuestro puente H como ejemplo para ilustrar este concepto:

\begin{figure}[H]
    \centering
    
    \caption{Nuestro Puente H}
    \label{fig:enter-label}
\end{figure}

En nuestro puente H, hemos separado las ramas del motor de las de control, ya que el motor opera con 24V DC y tiene una corriente eficaz de 3,5A. Para controlar el motor de manera eficiente, hemos optado por un diseño que incluye cuatro transistores MOSFET de potencia, los cuales pueden soportar picos de hasta 74A y 82A, garantizando que puedan manejar la corriente del motor de manera continua. Los MOSFET son IRF2805 (canal N) y IRF4905 (canal P). Además, los transistores son controlados mediante señales PWM, las cuales atraviesan un optoacoplador EL817 para minimizar el riesgo de que la corriente del motor regrese a la placa de control y cause daños. De ésta manera, podemos controlar el giro del motor de manera segura y regulada. 

La lógica de esta circuito se basa en que cuando un MOSFET canal P está saturado, el gate del MOSFET de canal N cruzado se activará. Cuando el MOSFET canal P no está saturado, el MOSFET cruzado canal N no se activará. El circuito cuenta con diodos Zener de 12 Volts para regular la tensión de Gate-Source en cada uno de los transistores, ya que el límite es de 20 Volts.

\subsection{Sistema de recepción de señales por UART}
El sistema de recepción de señales implementado en este proyecto se fundamenta en la transmisión de datos en formato JSON, el cual es enviado desde el microcontrolador RP2040 Zero hacia la Raspberry Pi 4, utilizando el protocolo de comunicación UART (Universal Asynchronous Receiver-Transmitter). Este esquema de transmisión de datos asíncrono es clave para garantizar la correcta transferencia de la información entre ambos dispositivos, especialmente en sistemas donde la baja latencia y la alta velocidad son factores cruciales.

Cuando la RP2040 Zero actúa como transmisor y envía datos a través del enlace UART, se introduce un optoacoplador de alta velocidad, el modelo 6N137. Este componente tiene como función principal aislar eléctricamente las dos partes del circuito, asegurando que las señales y alimentaciones de los dispositivos conectados permanezcan separadas. Esto no solo mejora la seguridad del sistema, sino que también protege los componentes sensibles de posibles interferencias o fluctuaciones de voltaje que podrían ocasionar fallas operativas o daños permanentes. El uso de optoacopladores es una práctica común en la ingeniería de control y automatización para proteger circuitos en entornos electromagnéticamente ruidosos.

Posteriormente, la señal transmitida es procesada mediante un transistor BJT (Bipolar Junction Transistor) del modelo 2N2222, que invierte la lógica de la señal. Esta operación es fundamental para garantizar que la interpretación de los datos sea precisa en el extremo receptor, adaptando la señal a los requerimientos lógicos de la Raspberry Pi 4.

Es importante destacar la elección de estos componentes electrónicos, especialmente por la alta tasa de transmisión que maneja el sistema UART, la cual opera a una velocidad de 115200 baudios. Esta velocidad de transmisión es adecuada para aplicaciones de tiempo real, donde se requiere una comunicación rápida y eficiente, sin comprometer la integridad de los datos transmitidos. El uso de componentes rápidos y confiables, como el optoacoplador 6N137 y el transistor 2N2222, asegura que el sistema pueda operar de manera estable y eficiente bajo estas condiciones.

\subsection{Control por PWM}
La modulación por ancho de pulso (PWM, por sus siglas en inglés Pulse Width Modulation) es una técnica empleada para regular la cantidad de energía suministrada a una carga, como un motor o un LED, mediante la variación del ciclo de trabajo de una señal pulsante. En lugar de modificar el voltaje de forma continua, PWM ajusta el tiempo durante el cual la señal permanece en estado alto (encendida) y bajo (apagada) dentro de un período fijo. Esto depende de los siguientes parámetros:

\begin{itemize}
    \item \textbf{Frecuencia:} Se refiere a la cantidad de ciclos de encendido y apagado que ocurren en un segundo, y se mide en Hertz (Hz).
    \item \textbf{Ciclo de trabajo:} Es el porcentaje de tiempo que la señal se mantiene en estado alto durante un ciclo. Por ejemplo:
    Un ciclo de trabajo del 0\% implica que la señal está siempre apagada.
    Un ciclo de trabajo del 50\% significa que la señal está encendida la mitad del tiempo y apagada la otra mitad.
    Un ciclo de trabajo del 100\% indica que la señal permanece siempre encendida.
    En nuestro proyecto, aplicamos la técnica de PWM en el control de los motores. Dado que utilizamos dos motores, si estos operaran a su máxima potencia, la silla de ruedas se desplazaría a una velocidad excesiva. Por esta razón, empleamos un ciclo de trabajo del 25\% para limitar la velocidad de avance.
\end{itemize}

\begin{figure}[H]
    \centering
    
    \caption{Ejemplo de señal PWM}
    \label{fig:enter-label}
\end{figure}

\subsection{Estructura de la silla}
La estructura de la silla de ruedas está compuesta por varios elementos fundamentales que aseguran su funcionamiento eficiente y seguro. En primer lugar, se encuentra un soporte robusto, cuyo propósito principal es sostener y estabilizar los motores que impulsan la silla. Este soporte ha sido diseñado para garantizar que los motores permanezcan firmemente sujetos, evitando vibraciones o movimientos indeseados que pudieran comprometer la precisión y fiabilidad del sistema.

El sistema de propulsión de la silla está constituido por dos motores de corriente continua (CC), cada uno operando a 24 voltios. Estos motores ofrecen una potencia promedio de 200W y alcanzan una potencia máxima de 500W. Este rango de potencia permite que la silla se desplace con suficiente fuerza para adaptarse a diversas condiciones de uso, ya sea en terrenos planos o en situaciones que requieran mayor esfuerzo.

En cuanto al asiento de la silla, ha sido confeccionado específicamente para este proyecto, integrando un diseño ergonómico que prioriza la comodidad del usuario sin sacrificar la funcionalidad. En la parte posterior del respaldo de la silla se encuentra una caja diseñada para actuar como una "Jaula de Faraday". Esta caja tiene la función de aislar eléctricamente los componentes electrónicos ubicados en su interior, protegiéndolos de interferencias electromagnéticas externas. 

\section{Desarrollo Técnico}
En este capítulo se proporcionará una descripción detallada sobre el funcionamiento de los distintos circuitos que conforman el dispositivo, así como su interacción en conjunto para cumplir con los objetivos del proyecto. Se explicará de manera clara y concisa cómo se utiliza el dispositivo, incluyendo instrucciones específicas para su correcto manejo y operatividad.

Además, se incluirán datos técnicos relevantes, tales como especificaciones de los componentes, características del diseño, y cualquier otro detalle que sea esencial para la comprensión del sistema. También se abordarán aspectos importantes acerca de las partes constitutivas del dispositivo, su función dentro del esquema general, y las consideraciones necesarias para su mantenimiento y optimización.

\subsection{Descripción del funcionamiento}
El usuario se sienta en la silla de ruedas y se coloca el dispositivo EEG. El EEG capta las señales cerebrales (alfa, beta, gamma, delta y theta) y las somete a un proceso de filtrado por hardware que incluye un filtro notch de 50 Hz, un filtro pasa-bajo de 100 Hz, un filtro pasa-alto de 0,5 Hz y un segundo filtro notch de 50 Hz. Posteriormente, las señales pasan por un circuito de compensación de offset para poder realizar la lectura por parte de la RP2040 Zero ya que la misma no puede leer valores negativos. Esta unidad se encarga de leer los datos mediante cuatro canales de ADC y enviarlos a la Raspberry Pi 4 por protocolo UART, donde se aloja el programa principal para el funcionamiento de la silla de ruedas.

Entre estos códigos se encuentran el control de motores, los filtros digitales, el procesamiento de señales y la inteligencia artificial (IA). Una vez las señales llegan a la Raspberry Pi 4, se filtran digitalmente para eliminar el ruido y mejorar la calidad de los datos. Tras el filtrado, las señales se envían a la IA, que tiene la función de reconocer los patrones cerebrales y determinar la dirección en la que el usuario desea moverse. Una vez el patrón ha sido identificado, se envía una señal a los motores para dirigir la silla hacia la dirección deseada (adelante, atrás, izquierda o derecha).

Además, el proyecto incluye un sistema de emergencia diseñado para garantizar la seguridad del usuario. Este sistema se activa si se detecta un error en la lectura de las señales o si hay un obstáculo en la trayectoria deseada. Su objetivo es prevenir accidentes y aumentar la seguridad del usuario al utilizar la silla de ruedas.

El sistema de emergencia utiliza sensores de ultrasonido para detectar la presencia de objetos a menos de 20 cm de la silla. En caso de detección, el sistema frena los motores y activa un LED en la dirección del objeto, además de un buzzer que emite una señal sonora durante un breve período para alertar al usuario sobre la activación del sistema.

\subsection{Funcionamiento del EEG}

El sistema de control de nuestra silla de ruedas se basa en el reconocimiento de señales cerebrales, lo que requiere un dispositivo especializado para captarlas: el electroencefalograma (EEG). Hemos desarrollado un EEG en forma de una cofia equipada con electrodos, los cuales se colocan siguiendo el protocolo conocido como “Sistema 10-20”. Este sistema estándar de ubicación define puntos específicos en el cuero cabelludo donde se deben colocar los electrodos para obtener lecturas óptimas de la actividad cerebral.

Los electrodos actúan como sensores pasivos que detectan las ondas cerebrales producidas por la actividad eléctrica del cerebro. Estas ondas se manifiestan como pequeñas fluctuaciones en el voltaje, que son captadas por los electrodos cuando se colocan sobre la superficie del cuero cabelludo del usuario. Es importante destacar que estos electrodos no penetran en el cráneo ni interactúan directamente con las neuronas. En cambio, registran los potenciales eléctricos generados por la actividad cerebral subyacente que se propagan hasta la superficie del cuero cabelludo.

Debido a que las señales captadas por los electrodos son de muy baja amplitud, requieren ser amplificadas antes de su procesamiento. Este paso no solo amplifica la señal cerebral, sino también el ruido presente en el entorno o generado por el propio cuerpo. Para abordar este problema, se realiza un proceso de filtrado que elimina el ruido y permite aislar las frecuencias relevantes de las ondas cerebrales. Para ello, utilizamos los AD620AN que son amplificadores de instrumento muy sensibles.

Las frecuencias de las ondas cerebrales detectadas son las siguientes:

\begin{itemize}
    \item Ondas alfa: 8-12 Hz
    \item Ondas beta: 12-30 Hz
    \item Ondas gamma: 30-100 Hz
    \item Ondas delta: 0,5-4 Hz
    \item Ondas theta: 4-8 Hz
\end{itemize}

Estas ondas cerebrales están asociadas con diferentes estados mentales y actividades cerebrales, por ejemplo, las ondas alfa se observan comúnmente en estados de relajación, mientras que las ondas beta se relacionan con un estado de alerta y concentración. Las ondas gamma, por otro lado, están vinculadas a procesos cognitivos de mayor complejidad, como la percepción y la conciencia. Las ondas delta y theta se asocian con fases profundas del sueño y la meditación.

\subsection{Funcionamiento de los filtros HardWare}

En un sistema de EEG, después de amplificar las señales captadas por los electrodos, se utilizan varios filtros para limpiar y mejorar la calidad de las señales antes de procesarlas o analizarlas. Estos filtros tienen un propósito importante: eliminar el ruido y enfocarse en las señales cerebrales relevantes. 

\subsubsection{Filtro Notch de 50 Hz}
\begin{itemize}
    \item \textbf{Propósito:} Atenuación del ruido inducido por la red eléctrica de 50 Hz, común en muchos sistemas de distribución de energía.
    \item \textbf{Funcionamiento:} El filtro Notch es un filtro de rechazo de banda estrecha, diseñado para eliminar una frecuencia específica (en este caso, 50 Hz) sin afectar significativamente las componentes de frecuencia cercanas o las señales EEG de interés. Las señales de EEG, que suelen estar en el rango de 0,5 a 40 Hz, pueden contaminarse por la interferencia de la red, por lo que este filtro resulta esencial para su eliminación sin alterar la información relevante.
\end{itemize}
\subsubsection{Filtro pasa bajos de 100 Hz}
\begin{itemize}
    \item \textbf{Propósito:} Reducción de las componentes de alta frecuencia que no son relevantes para el análisis EEG.
    \item \textbf{Funcionamiento:} Este filtro pasa bajos permite el paso de frecuencias inferiores a 100 Hz, atenuando aquellas que exceden este umbral. Las señales cerebrales de interés generalmente se sitúan por debajo de los 40 Hz, aunque algunas pueden extenderse hasta 100 Hz. Este filtro elimina frecuencias más altas, que usualmente corresponden a interferencias electromagnéticas, ruido de dispositivos electrónicos o artefactos musculares (EMG).
\end{itemize}
\subsubsection{Filtro pasa altos de 0,5 Hz}
\begin{itemize}
    \item \textbf{Propósito:} Eliminación de las componentes de muy baja frecuencia, incluyendo artefactos de corriente continua (DC) y ruido de baja frecuencia no relacionado con la actividad cerebral.
    \item \textbf{Funcionamiento:} El filtro pasa altos atenúa las señales con frecuencias por debajo de 0,5 Hz, permitiendo únicamente el paso de frecuencias superiores. La señal EEG relevante generalmente comienza en torno a los 0,5 Hz, mientras que frecuencias menores suelen estar asociadas a artefactos como el desplazamiento de los electrodos, fluctuaciones en la impedancia de los mismos, o interferencias lentas que no contienen información útil sobre la actividad cerebral.
\end{itemize}

\subsection{Funcionamiento de los filtros digitales}

Una vez que las ondas cerebrales son captadas y sometidas a un proceso inicial de filtrado, son transferidas a una Raspberry Pi 4. En este dispositivo se ejecuta un programa, desarrollado íntegramente por nuestro equipo, que continúa con el procesamiento y refinamiento de la señal. El motivo por el cual se aplica un filtrado adicional es que, luego de la etapa de filtrado inicial, la señal pasa por un segundo amplificador. Este amplificador, además de amplificar las señales cerebrales de interés, también amplifica el ruido residual presente en las mismas. Para contrarrestar este efecto, empleamos filtros digitales implementados por software, los cuales ofrecen una mayor precisión y control en la eliminación de interferencias no deseadas.

Dentro del programa, se han implementado los siguientes filtros:
\begin{itemize}
    \item \textbf{Filtro Notch de 50 Hz:} Este filtro está diseñado para eliminar las interferencias generadas por la red eléctrica, las cuales operan a una frecuencia de 50 Hz. Dado que estas interferencias pueden superponerse con la señal cerebral y distorsionar su interpretación, su eliminación es esencial para obtener un registro más fiel de la actividad cerebral.
    \item \textbf{Filtro Pasa-Bajo de 100 Hz:} El objetivo de este filtro es retener las frecuencias cerebrales más relevantes, es decir, aquellas que se encuentran por debajo de los 100 Hz, mientras que elimina el ruido de alta frecuencia, que suele ser resultado de interferencias externas o artefactos no relacionados con la actividad cerebral. Este rango incluye frecuencias relacionadas con ritmos cerebrales importantes como las ondas alfa, beta, y gamma.
    \item \textbf{Filtro Pasa-Alto de 0,5 Hz:} Este filtro se encarga de remover las señales de baja frecuencia que no aportan información útil sobre la actividad cerebral, como los artefactos causados por movimientos lentos o variaciones de corriente. Solo se permite el paso de las frecuencias EEG relevantes, garantizando que las señales reflejen con mayor precisión la actividad neural de interés.
\end{itemize}

Es importante señalar que el uso de estos filtros garantiza que la señal procesada esté lo más limpia posible de interferencias y artefactos, mejorando la precisión del sistema para detectar y procesar patrones cerebrales. La implementación de filtros mediante software, además, permite ajustar dinámicamente las configuraciones según las necesidades específicas del sistema y del entorno operativo, optimizando así el rendimiento de la silla de ruedas controlada por señales cerebrales.

\subsection{Funcionamiento del Puente H}

El circuito utiliza dos señales PWM (PWM1 y PWM2) para controlar los transistores MOSFET en configuración de puente H, lo que permite invertir la polaridad del voltaje aplicado al motor, controlando así la dirección de rotación. 

La velocidad del motor puede controlarse ajustando el ciclo de trabajo (duty cycle) de las señales PWM, que modulan la cantidad de energía entregada al motor.

Este circuito es ideal para aplicaciones donde se requiere un control preciso de dirección y velocidad de motores DC.

\subsubsection{Descripción de los Componentes}

\begin{enumerate}

    \item \textbf{U1 y U2 (PC817 - Optoacopladores):} Aíslan eléctricamente el circuito de control (de baja tensión) del circuito de potencia (de alta tensión). Esto protege al microcontrolador de posibles picos de voltaje y ruidos eléctricos provenientes del circuito de potencia.
    Cada optoacoplador tiene un LED interno que, al ser activado por una señal PWM, enciende un fototransistor interno, permitiendo que la señal de control pase al lado de potencia.
    
    \item \textbf{Q1 y Q3 (IRF4905 - MOSFET canal P):} Actúan como interruptores en la parte superior del puente H. Controlan la alimentación positiva hacia el motor. Estos MOSFET se activan cuando la señal PWM1 o PWM2 está en bajo (0V) y se desactivan cuando está en alto (señal de 5V), debido a la naturaleza de los MOSFET de canal P.
    
    \item \textbf{Q2 y Q4 (IRF2805 - MOSFET canal N):} Actúan como interruptores en la parte inferior del puente H. Conectan el motor a tierra cuando están activados. Estos MOSFET se activan cuando la señal PWM1 o PWM2 está en alto (5V) y se desactivan cuando está en bajo (0V).
    
    \item \textbf{R1 y R2 (Resistencias de 180 ohms):} Limitan la corriente de entrada hacia los LEDs internos de los optoacopladores (U1 y U2) para protegerlos de daños.
    
    \item \textbf{R3 y R4 (Resistencias de 1k ohms):} Están conectadas en serie con los MOSFET de canal P (Q1 y Q3). Limitan la corriente de la compuerta y aseguran un apagado rápido del MOSFET al detenerse la señal.
    
    \item \textbf{J1 y J2 (Conectores de entrada PWM):} Reciben las señales PWM de control provenientes de un microcontrolador o una fuente de señal PWM.
    
    \item \textbf{J3 y J4 (Conectores de alimentación):} Proveen la alimentación al circuito, uno con 24V para el motor y otro con 15V para los circuitos de control.
    
    \item \textbf{SW1 (Interruptor):}  utilizado para habilitar o deshabilitar el circuito completo, conectando o desconectando GND.
    
\end{enumerate}

\subsection{Funcionamiento del Sistema de Emergencia}
El sistema de emergencia de nuestra silla de ruedas controlada mediante señales cerebrales es un componente crítico para la seguridad del usuario, diseñado específicamente para evitar colisiones y accidentes en caso de que el usuario intente desplazarse hacia una dirección donde exista un obstáculo. Este sistema está integrado con los sensores ultrasónicos, que actúan como "ojos" del sistema, escaneando constantemente el entorno alrededor de la silla en cuatro direcciones: adelante, atrás, izquierda y derecha.

El funcionamiento es sencillo:
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

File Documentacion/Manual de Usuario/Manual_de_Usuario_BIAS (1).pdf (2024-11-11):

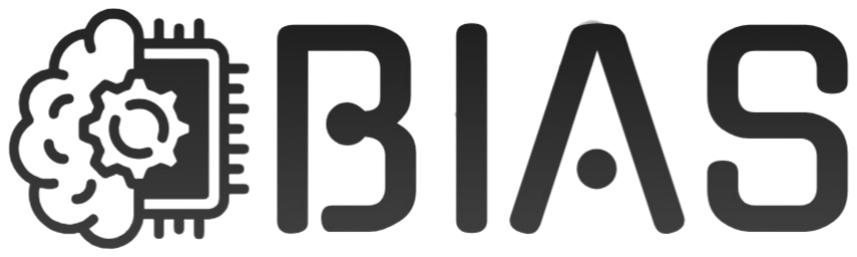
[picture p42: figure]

## Índice

1. Introduccion | 2
2. Precauciones Generales | 2
3. Descripcion del Sistema | 2
4. Instrucciones de Preparacion | 2
5. Uso de la Silla de Ruedas | 2
6. Mantenimiento y Cuidado | 3
7. Solucion de Problemas | 3
8. Preguntas Frecuentes (FAQ) | 4
9. Recursos Adicionales | 5

1

## 1. Introduccion

Bienvenido/a
Gracias por elegir nuestra silla de ruedas controlada mediante señales cerebrales. Este manual le guiará en los pasos para el correcto uso y la colocación de los electrodos de forma segura y efectiva.

## 2. Precauciones Generales

Use el dispositivo en un entorno controlado y seguro.

Verifique que todos los componentes estén en buen estado antes de cada uso.

No intente modificar el equipo.

## 3. Descripcion del Sistema

Este sistema utiliza un EEG de 9 electrodos que detectan señales cerebrales para controlar la dirección de la silla de ruedas. El dispositivo incluye un sistema de emergencia que se activa al detectar obstáculos.

## 4. Instrucciones de Preparacion

### 4.1. Colocacion de Electrodos

1. Preparación de la Piel

Limpie el cuero cabelludo para eliminar aceites y residuos.
Aplique una pequeña cantidad de pasta conductora en cada electrodo para luego colocarlo sobre el cuero cabelludo (asegurese de mover el pelo para que el electrodo toque la mayor cantidad de piel posible).
2. Posicionamiento de los Electrodos (Sistema 10-20):

Electrodo de Tierra: Coloque el electrodo de referencia (electrodo de color verde) en el lobulo de la oreja.
Electrodos de Señal:
- Coloque los electrodos de acuerdo a los puntos específicos designados en el EEG. Estos puntos son:
Para los electrodos positivos (electrodos de color rojo): C3, C4, Cz y Fc3
Para los electrodos negativos (electrodos de color negro): Fc1, Fc2, Pz, Fc4
- Asegure cada electrodo en su lugar sin que queden sueltos, para obtener una lectura de señal estable.
3. Revisión Final

Verifique que todos los electrodos estén bien conectados y que el sistema esté ajustado pero cómodo.

## 5. Uso de la Silla de Ruedas

### 5.1. Encendido del Sistema

1. Encienda la silla de ruedas y el EEG presionando los botones de encendido en ambos dispositivos.
2. Espere unos segundos mientras el sistema realiza las calibraciones iniciales.

2

### 5.2. Control de Movimientos

Relájese y concéntrese en pensar en los parametros de la siguiente tabla para poder moverse en la direccion deseada:

Movimiento a Pensar | Direccion hacia donde se mueve la silla
Pies | Adelante
Lengua | Atras
Mano izquierda | Izquierda
Mano derecha | Derecha

El sistema traducirá las señales cerebrales en movimiento hacia adelante, atrás, izquierda o derecha.

### 5.3. Sistema de Emergencia

1. En caso de detectar un obstáculo, la silla de ruedas se detendrá automáticamente.
2. Un indicador sonoro y visual (buzzer y LED) se activará si un obstáculo impide el movimiento en la dirección deseada.
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

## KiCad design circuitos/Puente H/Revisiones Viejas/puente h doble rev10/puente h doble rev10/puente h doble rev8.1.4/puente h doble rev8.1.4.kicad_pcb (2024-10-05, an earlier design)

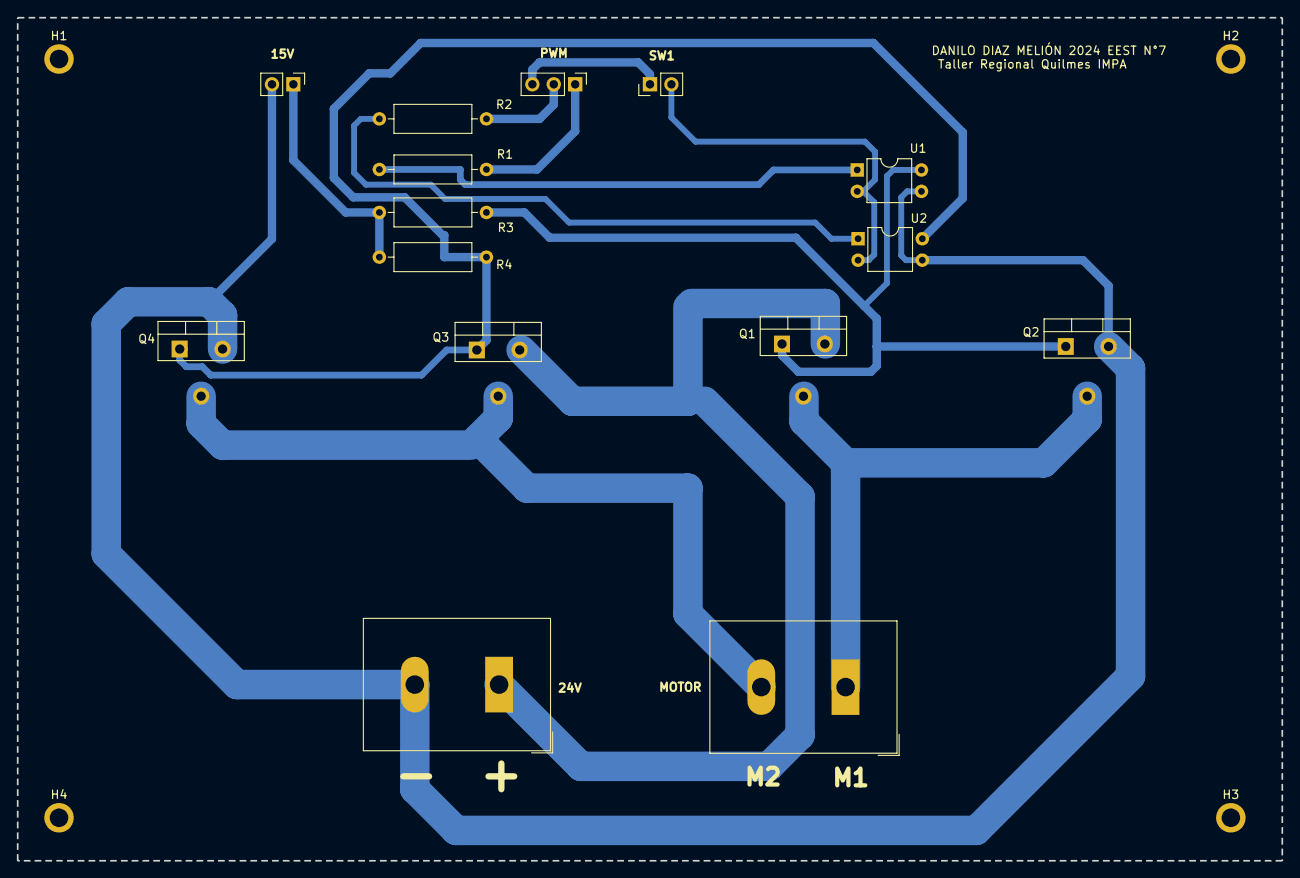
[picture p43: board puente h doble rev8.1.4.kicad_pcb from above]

Board: 2 copper layers, 150.0 x 100.0 mm, 19 parts (0 on the bottom side), 13 nets.

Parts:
15V: 15V Alimentación; PinHeader_1x02_P2.54mm_Vertical
24V: 24V Alimentación; TerminalBlock_Dinkle_DT-55-B01X-02_P10.00mm
H1, H2, H3, H4: MountingHole_2.2mm_M2_ISO7380_Pad
MOTOR: MOTOR; TerminalBlock_Dinkle_DT-55-B01X-02_P10.00mm
PWM: PWM; PinHeader_1x03_P2.54mm_Vertical
Q1, Q3: IRF4905; TO-220-3_Vertical
Q2, Q4: IRLZ44N; TO-220-3_Vertical
R1, R2: 180; R_Axial_DIN0309_L9.0mm_D3.2mm_P12.70mm_Horizontal
R3, R4: 1k; R_Axial_DIN0309_L9.0mm_D3.2mm_P12.70mm_Horizontal
SW1: SW; PinHeader_1x02_P2.54mm_Vertical
U1, U2: PC817; DIP-4_W7.62mm

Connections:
+15V: 15V.1, R3.1, R4.1
+24V: 24V.1, Q1.3 (S), Q3.3 (S)
GND: PWM.3, SW1.1 (A)
GNDPWR: 15V.2, 24V.2, Q2.3 (S), Q4.3 (S), U1.3, U2.3
unnamed: MOTOR.1, Q1.2 (D), Q2.2 (D)
unnamed: MOTOR.2, Q3.2 (D), Q4.2 (D)
unnamed: Q1.1 (G), Q2.1 (G), R3.2, U1.4
unnamed: Q3.1 (G), Q4.1 (G), R4.2, U2.4
unnamed: R1.2, U1.1
unnamed: R2.1, U2.1
unnamed: SW1.2 (B), U1.2, U2.2
PWM1: PWM.1, R1.1
PWM2: PWM.2, R2.2

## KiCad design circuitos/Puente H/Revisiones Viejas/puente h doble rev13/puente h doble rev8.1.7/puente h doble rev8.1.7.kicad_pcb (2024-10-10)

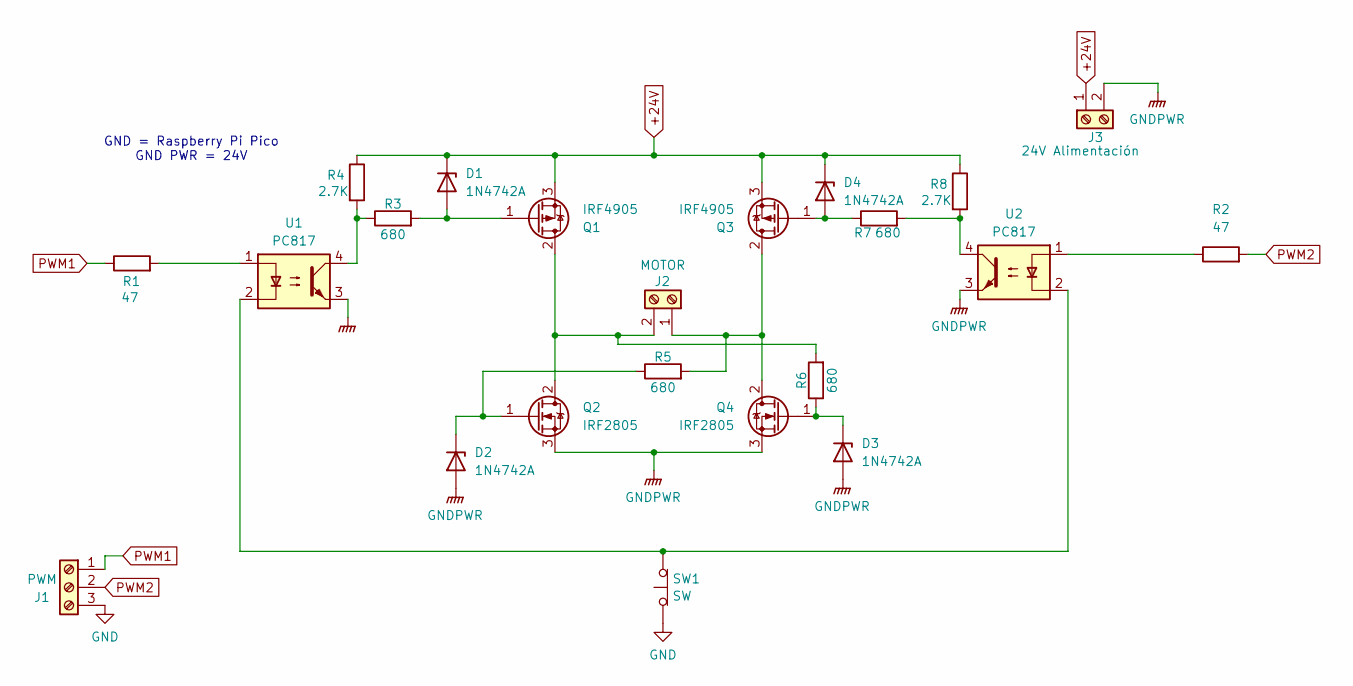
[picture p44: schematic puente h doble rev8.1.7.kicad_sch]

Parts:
D1, D2, D3, D4: 1N4742A; D_DO-41_SOD81_P10.16mm_Horizontal
J1: PWM; PinHeader_1x03_P2.54mm_Vertical
J2: MOTOR; TerminalBlock_Dinkle_DT-55-B01X-02_P10.00mm
J3: 24V Alimentación; TerminalBlock_Dinkle_DT-55-B01X-02_P10.00mm
Q1, Q3: IRF4905; TO-220-3_Vertical
Q2, Q4: IRF2805; TO-220-3_Vertical
R1, R2: 47; R_Axial_DIN0309_L9.0mm_D3.2mm_P12.70mm_Horizontal
R3, R5, R6, R7: 680; R_Axial_DIN0309_L9.0mm_D3.2mm_P12.70mm_Horizontal
R4, R8: 2.7K; R_Axial_DIN0309_L9.0mm_D3.2mm_P12.70mm_Horizontal
SW1: SW; PinHeader_1x02_P2.54mm_Vertical
U1, U2: PC817; DIP-4_W7.62mm

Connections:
+24V: D1.1 (K), D4.1 (K), J3.1, Q1.3 (S), Q3.3 (S), R4.1, R8.1
GNDPWR: D2.2 (A), D3.2 (A), J3.2, Q2.3 (S), Q4.3 (S), U1.3, U2.3
unnamed: D1.2 (A), Q1.1 (G), R3.2
unnamed: D2.1 (K), Q2.1 (G), R5.1
unnamed: D3.1 (K), Q4.1 (G), R6.1
unnamed: D4.2 (A), Q3.1 (G), R7.1
unnamed: J1.3, SW1.1 (A)
unnamed: J2.1, Q3.2 (D), Q4.2 (D), R5.2
unnamed: J2.2, Q1.2 (D), Q2.2 (D), R6.2
unnamed: R1.2, U1.1
unnamed: R2.1, U2.1
unnamed: R3.1, R4.2, U1.4
unnamed: R7.2, R8.2, U2.4
unnamed 14: SW1.2 (B), U1.2, U2.2; also elsewhere on the board
PWM1: J1.1, R1.1; also elsewhere on the board
PWM2: J1.2, R2.2; also elsewhere on the board

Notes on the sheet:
GND = Raspberry Pi Pico GND PWR = 24V

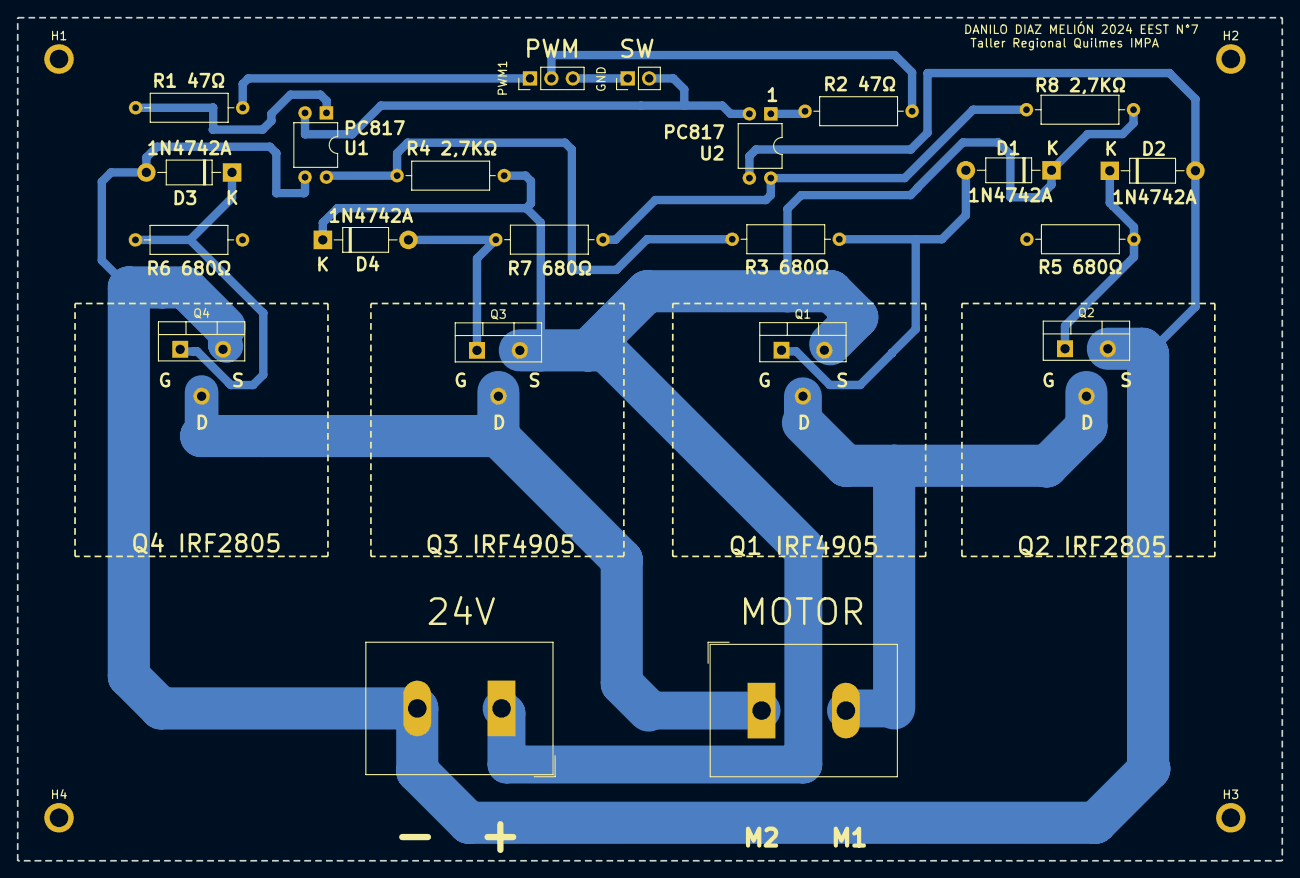
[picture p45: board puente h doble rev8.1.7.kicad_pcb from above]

Board: 2 copper layers, 150.0 x 100.0 mm, 26 parts (0 on the bottom side), 16 nets.

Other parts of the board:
GND: SW; PinHeader_1x02_P2.54mm_Vertical
H1, H2, H3, H4: MountingHole_2.2mm_M2_ISO7380_Pad
PWM1: PWM; PinHeader_1x03_P2.54mm_Vertical

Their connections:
GND: GND.1 (A), PWM1.3
unnamed 14: GND.2 (B); also elsewhere on the board
PWM1: PWM1.1; also elsewhere on the board
PWM2: PWM1.2; also elsewhere on the board

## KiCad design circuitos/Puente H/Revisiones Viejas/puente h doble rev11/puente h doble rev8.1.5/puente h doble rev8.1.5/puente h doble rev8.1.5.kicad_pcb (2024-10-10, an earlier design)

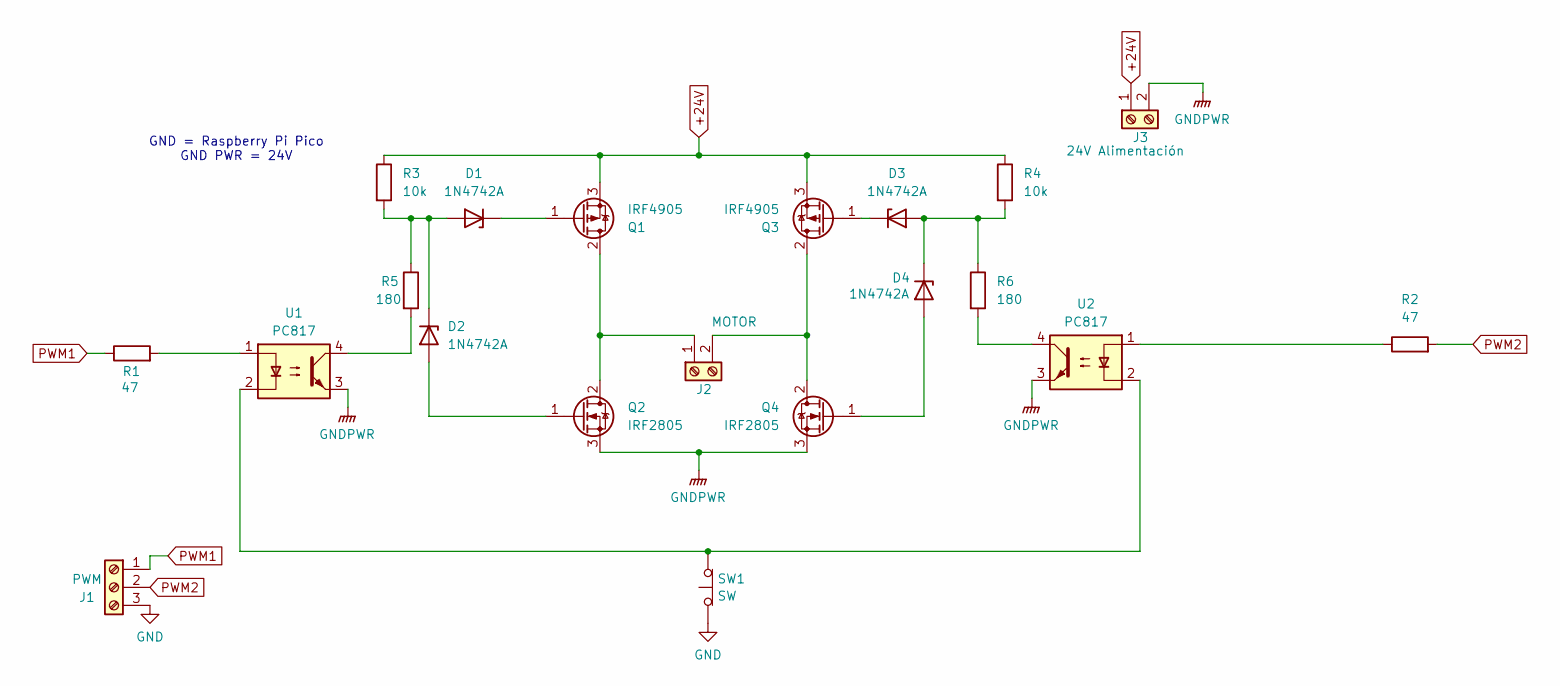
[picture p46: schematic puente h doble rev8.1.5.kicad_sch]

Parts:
D1, D2, D3, D4: 1N4742A; D_DO-41_SOD81_P10.16mm_Horizontal
J1: PWM; PinHeader_1x03_P2.54mm_Vertical
J2: MOTOR; TerminalBlock_Dinkle_DT-55-B01X-02_P10.00mm
J3: 24V Alimentación; TerminalBlock_Dinkle_DT-55-B01X-02_P10.00mm
Q1, Q3: IRF4905; TO-220-3_Vertical
Q2, Q4: IRF2805; TO-220-3_Vertical
R1, R2: 47; R_Axial_DIN0309_L9.0mm_D3.2mm_P12.70mm_Horizontal
R3, R4: 10k; R_Axial_DIN0309_L9.0mm_D3.2mm_P12.70mm_Horizontal
R5, R6: 180; R_Axial_DIN0309_L9.0mm_D3.2mm_P12.70mm_Horizontal
SW1: SW; PinHeader_1x02_P2.54mm_Vertical
U1, U2: PC817; DIP-4_W7.62mm

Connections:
+24V: J3.1, Q1.3 (S), Q3.3 (S), R3.1, R4.1
GND: J1.3, SW1.1 (A)
GNDPWR: J3.2, Q2.3 (S), Q4.3 (S), U1.3, U2.3
unnamed: D1.2 (A), D2.1 (K), R3.2, R5.1
unnamed: D1.1 (K), Q1.1 (G)
unnamed: D2.2 (A), Q2.1 (G)
unnamed: D3.2 (A), D4.1 (K), R4.2, R6.1
unnamed: D3.1 (K), Q3.1 (G)
unnamed: D4.2 (A), Q4.1 (G)
unnamed: J2.1, Q1.2 (D), Q2.2 (D)
unnamed: J2.2, Q3.2 (D), Q4.2 (D)
unnamed: R1.2, U1.1
unnamed: R2.1, U2.1
unnamed: R5.2, U1.4
unnamed: R6.2, U2.4
unnamed: SW1.2 (B), U1.2, U2.2
PWM1: J1.1, R1.1
PWM2: J1.2, R2.2

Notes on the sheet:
GND = Raspberry Pi Pico GND PWR = 24V

Board: 2 copper layers, 24 parts (0 on the bottom side), 18 nets, no tracks yet.

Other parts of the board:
H1, H2, H3, H4: MountingHole_2.2mm_M2_ISO7380_Pad

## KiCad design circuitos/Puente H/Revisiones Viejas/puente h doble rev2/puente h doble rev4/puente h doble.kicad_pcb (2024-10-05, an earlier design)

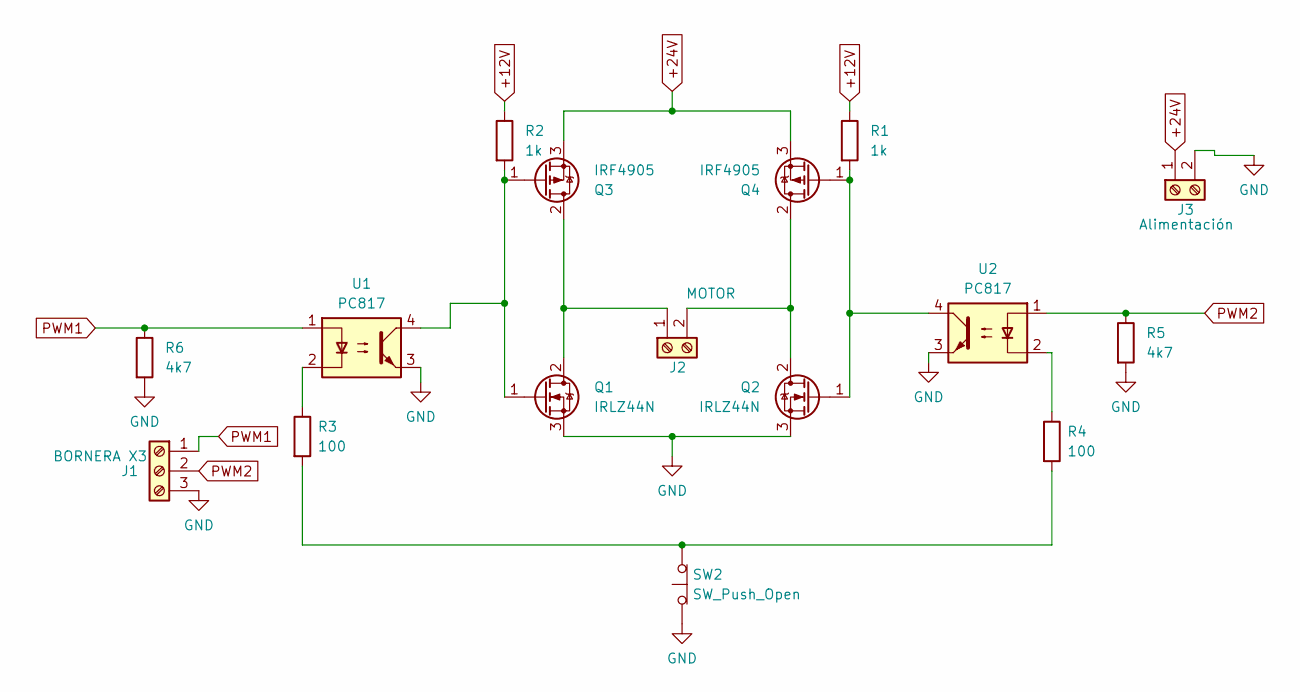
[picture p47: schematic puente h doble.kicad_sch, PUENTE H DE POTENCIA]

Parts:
J1: BORNERA X3; PinHeader_1x03_P2.54mm_Vertical
J2: MOTOR; TerminalBlock_Dinkle_DT-55-B01X-02_P10.00mm
J3: Alimentación; TerminalBlock_Dinkle_DT-55-B01X-02_P10.00mm
Q1, Q2: IRLZ44N; to-220 editado
Q3, Q4: IRF4905; to-220 editado
R1, R2: 1k; R_Axial_DIN0614_L14.3mm_D5.7mm_P20.32mm_Horizontal
R3, R4: 100; R_Axial_DIN0614_L14.3mm_D5.7mm_P20.32mm_Horizontal
R5, R6: 4k7; R_Axial_DIN0614_L14.3mm_D5.7mm_P20.32mm_Horizontal
SW2: SW_Push_Open; SW_CW_GPTS203211B
U1, U2: PC817; DIP-4_W7.62mm

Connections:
+12V: R1.1, R2.1
+24V: J3.1, Q3.3 (S), Q4.3 (S)
GND: J1.3, J3.2, Q1.3 (S), Q2.3 (S), R5.2, R6.2, SW2.1 (A), U1.3, U2.3
unnamed: J2.1, Q1.2 (D), Q3.2 (D)
unnamed: J2.2, Q2.2 (D), Q4.2 (D)
unnamed: Q1.1 (G), Q3.1 (G), R2.2, U1.4
unnamed: Q2.1 (G), Q4.1 (G), R1.2, U2.4
unnamed: R3.1, U1.2
unnamed: R4.1, U2.2
unnamed: R3.2, R4.2, SW2.2 (B)
PWM1: J1.1, R6.1, U1.1
PWM2: J1.2, R5.1, U2.1

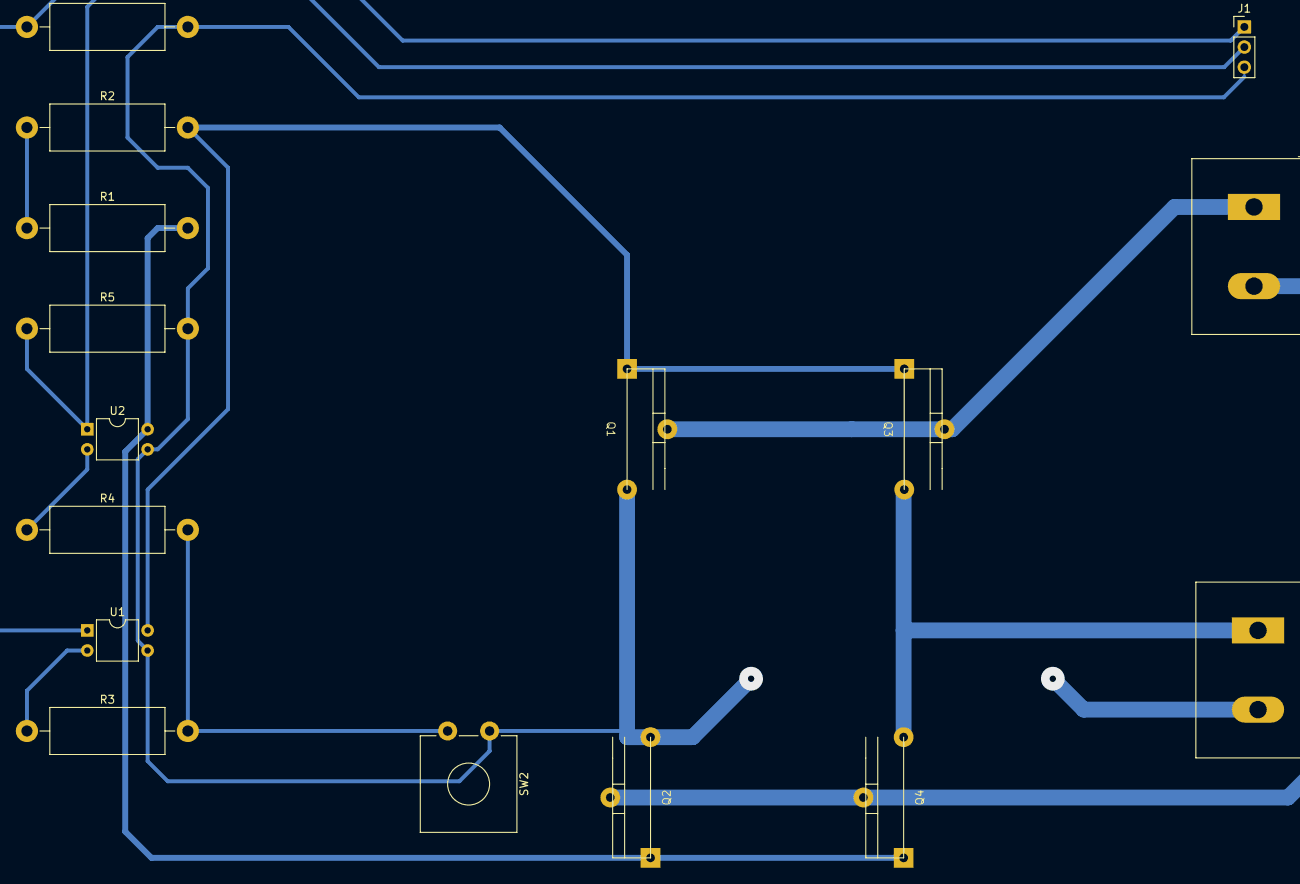
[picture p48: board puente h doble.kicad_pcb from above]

Board: 2 copper layers, 16 parts (0 on the bottom side), 12 nets.

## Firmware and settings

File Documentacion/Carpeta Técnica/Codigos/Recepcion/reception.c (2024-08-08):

#include <stdio.h>
#include <stdlib.h>
#include <string.h>
#include <math.h>
#include "pico/stdlib.h"
#include "hardware/uart.h"
#include "hardware/adc.h"

#define UART_ID uart0
#define BAUDRATE 115200
#define NUMBER_OF_CHANNELS 4
#define NUMBER_OF_TOTAL_SAMPLES 1000
#define ADC_DELAY_US -2000

// Value for conversion
const float CONVERSION_FACTOR = 3.3f * 1000 / (1 << 12);

// Array to store values of the samples
uint16_t values_mv[NUMBER_OF_CHANNELS][NUMBER_OF_TOTAL_SAMPLES];
// Flag of sampling done
static bool sampling_done = false;

// Funcion prototypes
void init_uart(uint8_t tx_pin, uint8_t rx_pin);
void init_adc(uint8_t adc_channel_0, uint8_t adc_channel_1, uint8_t adc_channel_2, uint8_t adc_channel_3);
bool read_adc(struct repeating_timer *t);
void start_sampling(void);
void build_json(char *data, uint total_bytes);
void send_data(char *data);

int main(void) {
    // Pins for ADC
    const uint8_t ADC_PIN_CHANNEL_0 = 26;
    const uint8_t ADC_PIN_CHANNEL_1 = 27;
    const uint8_t ADC_PIN_CHANNEL_2 = 28;
    const uint8_t ADC_PIN_CHANNEL_3 = 29;

    // Pins for UART
    const uint8_t UART_TX_PIN = 0;
    const uint8_t UART_RX_PIN = 1;

    // Amount of bytes to send
    uint TOTAL_BYTES_TO_SEND = sizeof("{}\n") // Considering null character
                               + (sizeof("\"ch0\":[],") - sizeof("")) * NUMBER_OF_CHANNELS // Excluding null character
                               + (sizeof("0000,") - sizeof("")) * NUMBER_OF_TOTAL_SAMPLES * NUMBER_OF_CHANNELS // Excluding null characters
                               - (NUMBER_OF_CHANNELS + 1); // Excluding commas

    // JSON data to send
    char data_to_send[TOTAL_BYTES_TO_SEND];

    stdio_init_all();
    // Initialize UART
    init_uart(UART_TX_PIN, UART_RX_PIN);
    // Initialize ADC
    init_adc(ADC_PIN_CHANNEL_0, ADC_PIN_CHANNEL_1, ADC_PIN_CHANNEL_2, ADC_PIN_CHANNEL_3);
    // Start the sampling
    start_sampling();

    while (true) {
        if (sampling_done) {
            //printf("Sampling done\n");
            // Make the JSON to send it
            build_json(data_to_send, TOTAL_BYTES_TO_SEND);
            //printf("JSON: %s\n", data_to_send);
            // Send the JSON
            send_data(data_to_send);
            // Clear sampling flag and restart sampling
            sampling_done = false;
            start_sampling();
        }
    }

    return 0;
}

void init_uart(uint8_t tx_pin, uint8_t rx_pin) {
    // UART setup
    uart_init(UART_ID, BAUDRATE);
    gpio_set_function(tx_pin, GPIO_FUNC_UART);
    gpio_set_function(rx_pin, GPIO_FUNC_UART);
    uart_set_format(UART_ID, 8, 1, UART_PARITY_NONE);
    uart_set_fifo_enabled(UART_ID, true);
}
void init_adc(uint8_t adc_channel_0, uint8_t adc_channel_1, uint8_t adc_channel_2, uint8_t adc_channel_3) {
    adc_init();
    // Initialize ADC channels
    adc_gpio_init(adc_channel_0);
    adc_gpio_init(adc_channel_1);
    adc_gpio_init(adc_channel_2);
    adc_gpio_init(adc_channel_3);
}

// Calback of the timer
bool read_adc(struct repeating_timer *t) {
    // Counter of sampling
    static uint sampling_count = 0;

    // Verify that the count doesn't exceed the total number of samples
    if (sampling_count >= NUMBER_OF_TOTAL_SAMPLES) {
        // Set the values after having completed the sampling
        sampling_done = true;
        cancel_repeating_timer(t);
        sampling_count = 0;
    } else {
        for (int channel = 0; channel < NUMBER_OF_CHANNELS; channel++) {
            // Read ADC channel
            adc_select_input(channel);
            uint16_t adc_value = adc_read();
            // Convert it to mV
            values_mv[channel][sampling_count] = round(adc_value * CONVERSION_FACTOR);
        }
        // Next sample
        sampling_count++;
    }
    return true;
}

void start_sampling(void) {
    // Start timer for sampling
    static struct repeating_timer timer;
    sampling_done = false;
    // Set the read_adc functon as callback with sample delay of 2000 us in order to have 500 Hz of sampling frequency
    add_repeating_timer_us(ADC_DELAY_US, read_adc, NULL, &timer);
}

// Function which transforms the adc_data to a JSON
void build_json(char *data, uint total_bytes) {
    // Stores the total number of bytes for the JSON
    char *str = (char*) malloc(total_bytes);
    if (str == NULL) {
        printf("Memory allocation failed\n");
        return;
    }

    strcpy(str, "{");
    // Print each value of the ADC channel until completing all channels with all the samplings
    for (int channel = 0; channel < NUMBER_OF_CHANNELS; channel++) {
        // Create the channel label
        char label[8];
        sprintf(label, "\"ch%d\":[", channel);

        // Concatenate the channel label to the JSON string
        strcat(str, label);

        // Create an auxiliary array
        char aux[sizeof("0000,")];

        // Print the values for the channel array
        for (int sampling_number = 0; sampling_number < NUMBER_OF_TOTAL_SAMPLES; sampling_number++) {
            if (sampling_number < NUMBER_OF_TOTAL_SAMPLES - 1) {
                sprintf(aux, "%d,", values_mv[channel][sampling_number]);
            } else {
                sprintf(aux, "%d", values_mv[channel][sampling_number]);
            }
            strcat(str, aux);
        }

        if (channel < NUMBER_OF_CHANNELS - 1) {
            strcat(str, "],");
        } else {
            strcat(str, "]}\n");
        }
    }
    strcpy(data, str);
    free(str);
}

// Send data by UART
void send_data(char *data) {
    uart_puts(UART_ID, data);
}


/*
// This code works
#include <stdio.h>
#include <stdlib.h>
#include <string.h>
#include <math.h>
#include "pico/stdlib.h"
#include "hardware/uart.h"
#include "hardware/adc.h"

#define UART_ID uart0
#define BAUDRATE 115200
#define NUMBER_OF_CHANNELS 4
#define NUMBER_OF_TOTAL_SAMPLES 1000
#define ADC_DELAY_US -2000

// Value for conversion
const float CONVERSION_FACTOR = 3.3f * 1000 / (1 << 12);

// Array to store values of the samples
uint16_t values_mv[NUMBER_OF_TOTAL_SAMPLES][NUMBER_OF_CHANNELS];
// Flag of sampling done
static bool sampling_done = false;

// Funcion prototypes
void init_uart(uint8_t tx_pin, uint8_t rx_pin);
void init_adc(uint8_t adc_channel_0, uint8_t adc_channel_1, uint8_t adc_channel_2, uint8_t adc_channel_3);
bool read_adc(struct repeating_timer *t);
void start_sampling(void);
void build_json(char *data, uint total_bytes);
void send_data(char *data);

int main(void) {
    // Pins for ADC
    const uint8_t ADC_PIN_CHANNEL_0 = 26;
    const uint8_t ADC_PIN_CHANNEL_1 = 27;
    const uint8_t ADC_PIN_CHANNEL_2 = 28;
    const uint8_t ADC_PIN_CHANNEL_3 = 29;

    // Pins for UART
    const uint8_t UART_TX_PIN = 0;
    const uint8_t UART_RX_PIN = 1;

    // Amount of bytes to send
    uint TOTAL_BYTES_TO_SEND = sizeof({}) + sizeof("\"s000\":[0000,0000,0000,0000],") * NUMBER_OF_TOTAL_SAMPLES;

    // JSON data to send
    char data_to_send[TOTAL_BYTES_TO_SEND];

    stdio_init_all();
    // Initialize UART
    init_uart(UART_TX_PIN, UART_RX_PIN);
    // Initialize ADC
    init_adc(ADC_PIN_CHANNEL_0, ADC_PIN_CHANNEL_1, ADC_PIN_CHANNEL_2, ADC_PIN_CHANNEL_3);
    // Start the sampling
    start_sampling();

    while (true) {
        if (sampling_done) {
            //printf("Sampling done\n");
            // Make the JSON to send it
            build_json(data_to_send, TOTAL_BYTES_TO_SEND);
            //printf("%s", data_to_send);
            // Send the JSON
            send_data(data_to_send);
            // Clear sampling flag and restart sampling
            sampling_done = false;
            start_sampling();
        }
    }

    return 0;
}

void init_uart(uint8_t tx_pin, uint8_t rx_pin) {
    // UART setup
    uart_init(UART_ID, BAUDRATE);
    gpio_set_function(tx_pin, GPIO_FUNC_UART);
    gpio_set_function(rx_pin, GPIO_FUNC_UART);
    uart_set_format(UART_ID, 8, 1, UART_PARITY_NONE);
    uart_set_fifo_enabled(UART_ID, true);
}
void init_adc(uint8_t adc_channel_0, uint8_t adc_channel_1, uint8_t adc_channel_2, uint8_t adc_channel_3) {
    adc_init();
    // Initialize ADC channels
    adc_gpio_init(adc_channel_0);
    adc_gpio_init(adc_channel_1);
    adc_gpio_init(adc_channel_2);
    adc_gpio_init(adc_channel_3);
}

// Calback of the timer
bool read_adc(struct repeating_timer *t) {
    // Counter of sampling
    static uint sampling_count = 0;

    // Verify that the count don't exceed the total number of samples
    if (sampling_count >= NUMBER_OF_TOTAL_SAMPLES) {
        sampling_done = true;
        cancel_repeating_timer(t);
        sampling_count = 0;
    } else {
        for (int channel = 0; channel < NUMBER_OF_CHANNELS; channel++) {
            // Read ADC channel
            adc_select_input(channel);
            uint16_t adc_value = adc_read();
            // Convert it to mV
            values_mv[sampling_count][channel] = round(adc_value * CONVERSION_FACTOR);
        }
        sampling_count++;
    }
    return true;
}

void start_sampling(void) {
    // Start timer
    static struct repeating_timer timer;
    sampling_done = false;
    // Set the read_adc functon as callback with sample delay of 2000 us in order to have 500 Hz of sampling frequency
    add_repeating_timer_us(ADC_DELAY_US, read_adc, NULL, &timer);
}

void print_adc_values(void) {
    for (int sampling_number = 0; sampling_number < NUMBER_OF_TOTAL_SAMPLES; sampling_number++) {
        for (int channel = 0; channel < NUMBER_OF_CHANNELS; channel++) {
            printf("values_mv[%d][%d]: %d; ", sampling_number, channel, values_mv[sampling_number][channel]);
        }
    }
}

// Function which transforms the adc_data to a JSON
void build_json(char *data, uint total_bytes) {
    // Stores the total number of bytes for the JSON
    char *str = (char*) malloc(total_bytes);
    if (str == NULL) {
        printf("Memory allocation failed\n");
        return;
    }

    sprintf(str, "{");
    // Print each value of the ADC channel until completing all the samplings
    for (int sampling_number = 0; sampling_number < NUMBER_OF_TOTAL_SAMPLES; sampling_number++) {
        char aux[30];

        // Check if it isn't the last one
        if (sampling_number < NUMBER_OF_TOTAL_SAMPLES - 1) {
            sprintf(aux, "\"s%d\":[%d,%d,%d,%d],", sampling_number, values_mv[sampling_number][0], 
            values_mv[sampling_number][1], values_mv[sampling_number][2], values_mv[sampling_number][3]);
        } else {
            sprintf(aux, "\"s%d\":[%d,%d,%d,%d]", sampling_number, values_mv[sampling_number][0], 
            values_mv[sampling_number][1], values_mv[sampling_number][2], values_mv[sampling_number][3]);
        }
        // Concatenate the auxiliary string
        strcat(str, aux);
    }
    // Concatenate the end of line to detect the end of the JSON
    strcat(str, "}\n");
    strcpy(data, str);
    free(str);
}

// Send data by UART
void send_data(char *data) {
    uart_puts(UART_ID, data);
}

*/

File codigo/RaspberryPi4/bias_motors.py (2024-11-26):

from gpiozero import DistanceSensor, PWMLED, Buzzer, PWMOutputDevice
from gpiozero.pins.pigpio import PiGPIOFactory
import time

def main():
    # Define motor instance
    biasMotor = MotorBias(echo_forward=18, trigger_forward=17, echo_backwards=23, trigger_backwards=22, echo_right=5, trigger_right=6,
                          echo_left=25, trigger_left=24, led_forward=16, led_backwards=20, led_left=21, led_right=26, buzzer=12, motor1_in1=13,
                          motor1_in2=19, motor2_in1=7, motor2_in2=8)

    biasMotor.brake()

    while True:
        # Get command
        command = input("Enter command (forward/left/backwards/right/stop): ").strip()
        biasMotor.move_if_possible(command)

class MotorBias:
    def __init__(self, echo_forward, trigger_forward, echo_backwards, trigger_backwards, echo_right, trigger_right,
                 echo_left, trigger_left, led_forward, led_backwards, led_left, led_right, buzzer, motor1_in1,
                 motor1_in2, motor2_in1, motor2_in2):

        # Set up pin factory in order to use pigpio
        factory = PiGPIOFactory()

        # Configure ultrasonic sensors and LEDs
        self._ultrasonic_forward = DistanceSensor(echo=echo_forward, trigger=trigger_forward, pin_factory=factory)
        self._ultrasonic_backwards = DistanceSensor(echo=echo_backwards, trigger=trigger_backwards, pin_factory=factory)
        self._ultrasonic_right = DistanceSensor(echo=echo_right, trigger=trigger_right, pin_factory=factory)
        self._ultrasonic_left = DistanceSensor(echo=echo_left, trigger=trigger_left, pin_factory=factory)

        # Configure LEDs
        self._led_forward = PWMLED(led_forward, pin_factory=factory)
        self._led_backwards = PWMLED(led_backwards, pin_factory=factory)
        self._led_left = PWMLED(led_left, pin_factory=factory)
        self._led_right = PWMLED(led_right, pin_factory=factory)

        # Configure buzzer
        self._buzzer = Buzzer(buzzer)

        # GPIO Pin setup for Motor 1
        self._motor1_in1 = PWMOutputDevice(motor1_in1, initial_value=0,  frequency=50, pin_factory=factory)
        self._motor1_in2 = PWMOutputDevice(motor1_in2, initial_value=0, frequency=50, pin_factory=factory)

        # GPIO Pin setup for Motor 2
        self._motor2_in1 = PWMOutputDevice(motor2_in1, initial_value=0, frequency=50, pin_factory=factory)
        self._motor2_in2 = PWMOutputDevice(motor2_in2, initial_value=0, frequency=50, pin_factory=factory)

    def move_if_possible(self, command):
        try:
            distance = 30
            # Move forward
            if command == "forward":
                #distance = self._ultrasonic_forward.distance * 100
                # Maximum distance of 20 cm
                if distance < 20:
                    # Forward is blocked
                    self._led_forward.on()
                    self._buzzer.on()
                    print(f"Obastacle forward: {distance:.1f} cm. Blocked movement.")
                else:
                    print("Going forward")
                    # Do the movement
                    self._led_forward.off()
                    self._buzzer.off()
                    self.move_forward(25)
            # Move backwards
            elif command == "backwards":
                #distance = self._ultrasonic_backwards.distance * 100
                # Maximum distance of 20 cm
                if distance < 20:
                    # Backwards is blocked
                    self._led_backwards.on()
                    self._buzzer.on()
                    print(f"Obstacle backwards: {distance:.1f} cm. Blocked movement.")
                else:
                    print("Going backwards")
                    # Do the movement
                    self._led_backwards.off()
                    self._buzzer.off()
                    self.move_backward(25)
            # Turn left
            elif command == "left":
                #distance = self._ultrasonic_left.distance * 100
                # Maximum distance of 20 cm
                if distance < 20:
                    # Left is blocked
                    self._led_left.on()
                    self._buzzer.on()
                    print(f"Obstacle on the left: {distance:.1f} cm. Blocked movement")
                else:
                    print("Turning left")
                    # Do the movement
                    self._led_left.off()
                    self._buzzer.off()
                    self.turn_left(25)
            # Turn right
            elif command == "right":
                #distance = self._ultrasonic_right.distance * 100
                # Maximum distance of 20 cm
                if distance < 20:
                    # Right is blocked
                    self._led_right.on()
                    self._buzzer.on()
                    print(f"Obstacle on the right: {distance:.1f} cm. Blocked movement.")
                else:
                    print("Turning right")
                    # Do the movement
                    self._led_right.off()
                    self._buzzer.off()
                    self.turn_right(25)
            # Brake
            elif command == "stop":
                print("Stopping")
                # Make all parameters off
                self.brake()
                self._led_forward.off()
                self._led_backwards.off()
                self._led_left.off()
                self._led_right.off()
                self._buzzer.off()
            else:
                print("Invalid command")

            time.sleep(1)
            self.brake() # Stop after each command
            self._led_forward.off()
            self._led_backwards.off()
            self._led_left.off()
            self._led_right.off()
            self._buzzer.off()


        except KeyboardInterrupt:
            self.brake()
            print("Program stopped by user")

    # Configure speed of motor depending on PWM
    def set_motor_speed(self, motor_in1, motor_in2, speed):
        # Define positive speed
        if speed > 0:
            motor_in2.value = 0
            if motor_in2.value == 0:
                motor_in1.value = speed / 100.0
            print(motor_in1.value)
            print(motor_in2.value)

        # Define negative speed
        elif speed < 0:
            motor_in1.value = 0
            if motor_in1.value == 0:
                motor_in2.value = abs(speed) / 100.0
            print(motor_in1.value)
            print(motor_in2.value)
        # If it's zero brake
        else:
            motor_in1.value = 0
            motor_in2.value = 0
            print(motor_in1.value)
            print(motor_in2.value)

    # Move wheelchair forward
    def move_forward(self, speed):
        self.set_motor_speed(self._motor1_in1, self._motor1_in2, speed)
        self.set_motor_speed(self._motor2_in1, self._motor2_in2, speed)
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

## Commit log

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2024-06-05 fix: arreglar tiempo ya que las señales no correspondían a su forma
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2024-06-08 fix: arreglar función i2c_slave_handler
2024-06-08 fix: modificación del código ya que el ADC contiene dos bytes
2024-06-08 fix: modificar código de Micropython a Python
2024-06-08 fix: modificar para lectura de ADC
2024-06-09 fix: la Pi 4 no permite joystick porque no tiene ADC
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2024-06-11 fix: arreglar bugs debido a código redundante
    [reception.c]
2024-06-21 fix: fix the bugs on filtering
2024-06-21 fix: change the timer so th sampling frequency could be achieved
2024-06-21 fix: read four channels of ADC and then they would be combined
2024-07-02 fix: debugging of i2c
    [reception.c]
2024-07-04 fix: Connect RP2040 with Raspberry Pi 4 via I2C
    [reception.c]
2024-07-06 fix: debugging with printing for i2c connection
    [reception.c]
2024-07-31 style: add a comment
    [pyvenv.cfg]
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2024-08-03 fix: communication by UART
    I2C was not the best choice to send data. For this reason we decided to use UART as the alternative
    [reception.c]
2024-08-06 fix: data can be sent by UART
    [reception.c]
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2024-08-19 fix: correct bugs while plotting signals
    [app.py]
2024-08-21 fix: modify reduced variables
    [bias_dsp.py]
2024-08-22 fix: change graphing moment
    [bias.py, bias_dsp.py]
2024-08-23 feat: se añadio main3
    es el codigo unido del main con el del puente H. se le añadio los leds y los demas ultrasonidos
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2024-08-23 fix: change class order so that it's clearer
    [bias_ai.py]
2024-08-27 feat:; add PWM inverted output
    [bias_motors.py]
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2024-08-28 fix: change values so that it could work in reality
    [bias_motors.py]
2024-09-01 fix: change Bias class name for circular error
    [app.py, bias.py, bias_ai.py]
2024-09-01 fix: change format of synthetic data
    [bias_ai.py]
2024-09-01 fix: adjust dimention of input layer
    [bias_ai.py]
2024-09-02 fix: change name variable
    [app.py, bias_ai.py]
2024-09-03 fix: assert that list has certain requirements
    [bias_ai.py]
2024-09-03 fix: assert data makes sense
    [bias_ai.py]
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2024-09-04 feat: se añaden 3 codigos para el multithreading
    con el run_task.py se ejecutan los dos codigos
2024-09-06 fix: change libraries imported names
    [app.py]
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2024-09-13 feat: otro arreglo de codigo
    [app.py, motor_task.py]
2024-09-19 feat: Subida de contenido de la carpeta técnica
    Aqui se adjuntaron todas las imágenes y códigos que están hasta el momento en la carpeta técnica
2024-09-20 fix: fix errors and delete folder with dataset referring to a repository
    [bias_dsp.py, bias_reception.py]
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2024-09-23 fix: correccion de nombre de carpeta "docs" a "circuitos"
2024-09-23 fix: cambio de nombre a carpeta "PDFs EEG" a filtrosEEG
2024-09-23 Feat: Creacion de Carpetas "DLCs Kicad" y "SistemaOffset" ; Agregado del archivo de bornera KF301-3P en un comprimido
2024-09-23 feat: agregado el archivo del modelo de bornera KF301-2P en comprimido para Kicad
2024-09-23 Feat: Agregado el archivo del modelo del Operacional TL084 para Kicad en comprimido
2024-09-23 Feat: Agregado del archivo del modelo del Regulador LM7805 para Kicad en Comprimido
2024-09-23 Feat: Agregado del archivo del modelo del amplificador AD620AN para Kicad en Comprimido
2024-09-23 Feat: Agregado del archivo de modelos de Jumpers para Kicad en comprimido
2024-09-23 Feat: Agregado del archivo del modelo del Micro RP2040zero para Kicad en Comprimido
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2024-09-23 feat: agregado del archivo del Micro RPBRRY Pi4 para Kicad en comprimido
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2024-09-23 feat: creacion carpeta Serigrafia
    se incluye el archivo del modeo del Logo del proyecto para Kicad en comprimido
2024-09-23 feat: creacion de seccion simulacion de circuitos
    se incluye subseccion (carpeta) de filtro EEG que incluye la simulacion del circuito de los amplificadores
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2024-09-25 feat: Actualización de carpeta técnica
    Añadido: Explicación de Jaula de Faraday y su aplicación
2024-09-25 feat: Explicación Puente H
    Se añadió la explicación teórica del Puente H, su aplicación e Imágenes.
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2024-09-26 feat: añadir revisión 1 de puente h doble
    [puente h doble.kicad_pcb, puente h doble.kicad_sch]
2024-09-27 fix: not compiling code
    [bci_iv_2a.py, bias_reception.py]
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2024-09-30 fix: change number of samples in the dataset
    [bci_iv_2a.py]
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2024-09-30 fix: change incoherent dimentions
    [bci_iv_2a.py, bias_ai.py]
2024-09-30 fix: modify num of features
    [bci_iv_2a.py, bias_ai.py]
2024-09-30 fix: organizacion de carpeta
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2024-10-04 fix: eliminar el manual tecnico bugeado
2024-10-04 fix: modify iteration in the dataset
    [bci_iv_2a.py, bias_ai.py]
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2024-10-04 fix: prepare dataset to be trained
    [bci_iv_2a.py, bias_ai.py]
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2024-10-04 fix: change variables name
    [bci_iv_2a.py]
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2024-10-05 feat: añadir revisión vieja del puente H en KiCad
    [puente h doble.kicad_pcb, puente h doble.kicad_sch]
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2024-10-05 feat: añadir revisión n°4 de puente H en kicad
    [puente h doble rev5.kicad_pcb, puente h doble rev5.kicad_sch, puente h doble.kicad_pcb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]
2024-10-05 feat: añadir revisión n°5 del puente H kicad
    [puente h doble rev5.kicad_pcb, puente h doble rev5.kicad_sch, puente h doble.kicad_pcb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]
2024-10-05 feat: añadir revisión n°6 del puente H kicad
    [puente h doble rev5.kicad_pcb, puente h doble rev5.kicad_sch, puente h doble.kicad_pcb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]
2024-10-05 feat: añadir revisión n°7 del puente H kicad
    [puente h doble rev8.kicad_pcb, puente h doble rev8.kicad_sch]
2024-10-05 feat: añadir revisión n°8 del puente H kicad
    [puente h doble rev8.1.2.kicad_pcb, puente h doble rev8.kicad_pcb, puente h doble rev8.kicad_sch]
2024-10-05 feat: añadir revisión n°9 del puente H kicad
    [puente h doble rev8.1.3.kicad_pcb, puente h doble rev8.1.3.kicad_sch]
2024-10-05 feat: añadir revisión n°10 del puente H kicad
    [disipador_to220.STEP, puente h doble rev8.1.4.kicad_pcb, puente h doble rev8.1.4.kicad_sch]
2024-10-07 fix: combine all trials for 9 datasets
    [bci_iv_2a.py]
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2024-10-10 feat: añadir revisión 11 del Puente H
    [User Library-TO220-A PCB ga1.step, User Library-TO220-A PCB ga2.stl, disipador_to220.STEP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]
2024-10-10 feat: añadir revisión 13 puente h
    [User Library-TO220-A PCB ga1.step, User Library-TO220-A PCB ga2.stl, disipador_to220.STEP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]
2024-10-10 feat: añadir revisión 14 puente h
    [User Library-TO220-A PCB ga1.step, User Library-TO220-A PCB ga2.stl, disipador_to220.STEP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]
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2024-10-10 fix: change segmentation function
    [bci_iv_2a.py]
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2024-10-10 fix: modify dimention of layer
    [bci_iv_2a.py]
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2024-10-12 fix: modify svm algorithm
    [bci_iv_2a.py]
2024-10-12 fic: solve compiling error
    [bci_iv_2a.py]
2024-10-12 fix: change dimentionality of features
    [bias_ai.py]
2024-10-12 fix: change parameters which didn't allow to compile
    [bci_iv_2a.py, bias_ai.py, bias_dsp.py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]
2024-10-12 fix: change label binarizer
    [bci_iv_2a.py, bias_ai.py, bias_motors.py]
2024-10-13 fix: make system work
    [bci_iv_2a.py, bias.py, bias_dsp.py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]
2024-10-13 fix: modify get_real_data function
    [bci_iv_2a.py, bias_ai.py, bias_dsp.py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]
2024-10-13 fix: change signal dimention
    [bias_dsp.py]
2024-10-13 fix: Correcion de errores ortograficos y gramaticos
2024-10-14 fix: corregir informacion sobre el proyecto erronea
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2024-10-14 fix: corregir informe de puente H con el modelo actualizado
2024-10-19 fix: modify compiling errors
    [bci_iv_2acnn.py, bias.py, bias_ai.py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]
2024-10-22 fix: change initial value of PWM
    [bias.py, bias_motors.py, bias_reception.py]
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2024-10-29 feat: añadir plano autocad de parte baja de gabinete del puente h
    [ParteBajaGabinete.dwg]
2024-10-29 feat: añadir plano autocad de tapa de gabinete del puente h
    [ParteArribaGabinete.dwg]
2024-10-29 feat: añadir plano autocad de costado corto de gabinete del puente h
    [CostadoCortoGabinete.dwg]
2024-10-29 feat: añadir plano autocad de costado largo de gabinete del puente h
    [CostadoLargoGabinete.dwg]
2024-10-29 feat: añadir plano autocad de varilla para disipadores del puente H
    [SoporteGabinete.dwg]
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2024-10-29 fix: eliminar informe de Puente H desactualizado
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2024-10-31 fix: modify motors code
    [bci_iv_2acnn.py, bias_dsp.py, bias_motors.py]
2024-10-31 fix: set frequency in reception to 250 Hz
    [reception.c]
2024-11-04 feat: Organizacion de la carpeta Modelado 3D
    [SistemaEmergenciasFull.dwg, center-front.stl, left-front.stl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]
2024-11-04 feat: Costado.stl
    [Costado.stl]
2024-11-04 feat: Parte frontal inferior
    [ParteFrontalInferior.stl]
2024-11-04 feat: Parte frontal superior
    [ParteFrontalSuperior.stl]
2024-11-04 feat: Parte inferior
    [ParteInferior.stl]
2024-11-04 feat: Parte superior 1
    [ParteSuperior1.stl]
2024-11-04 feat: Parte superior 2
    [ParteSuperior2.stl]
2024-11-04 feat: Parte trasera
    [ParteTrasera.stl]
2024-11-05 fix: ordenar los archivos 3D
    [CostadoCortoGabinete.dwg, CostadoLargoGabinete.dwg, ParteArribaGabinete.dwg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]
2024-11-05 feat: Corrección de ParteTrasera.stl
    [ParteTrasera.stl]
2024-11-06 feat: Corrección de dos modelos y STLs
    [CostadoLargoBornerasGabinete.dwg, CostadoLargoGabinete.dwg, CostadoLargoPinesGabinete.dwg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]
2024-11-06 feat: STLs
    [ParteArribaGabinete.stl]
2024-11-06 feat: Soporte STL
    [SoporteGabinete.stl]
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2024-11-07 Fix: Carpeta de mas Recepcion y alimentacion
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2024-11-08 Fix: arreglo de R en Offset
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2024-11-27 fix: reorganizar carpeta Modelado 3D
    [Costado.stl, CostadoCortoGabinete.dwg, CostadoCortoGabinete.stl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]
2024-11-27 feat: FACTURA BIAS
    [Costado.stl, CostadoCortoGabinete.dwg, CostadoCortoGabinete.stl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]
